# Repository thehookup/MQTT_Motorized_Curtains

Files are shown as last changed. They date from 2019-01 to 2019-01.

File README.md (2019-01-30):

# MQTT_Motorized_Curtains
Stepper motor controlled MQTT curtains - Home Assistant Integrated

## Initial Setup

1. Download the .ino file
2. Ensure you have the correct libraries download and installed (links at top of the ino file)
3. Update information in the user configuration section and upload to the NodeMCU
4. Hook up your NodeMCU, stepper driver and motor as shown in the wiring section
5. Send a value of 0 to the position MQTT topic which will be:

```c++
[USER_MQTT_CLIENT_NAME]/positionCommand
```
6. Send incrementally higher values to the position MQTT topic until your blinds are fully closed
7. Input that position value into the STEPS_TO_CLOSE field in the arduino sketch.
8. Send the updated file to your NodeMCU.

## Parts (Amazon Links)

Stepper Package 	        https://amzn.to/2MpRQPu

Pulleys	 	                https://amzn.to/2FLbCDI

Curtain Rope		          https://amzn.to/2U7h5Zs

Extruder Gear	 	          https://amzn.to/2T4QtrL

Bearings		              https://amzn.to/2U4bdQI

NodeMCU	                	https://amzn.to/2MkBcka

Buck Converter	 	        https://amzn.to/2FEcNFF

Power Supply		          https://amzn.to/2MmtFBj

M3 x 20mm	       	        Home Depot

#10 bolt	       	        Home Depot

## Wiring

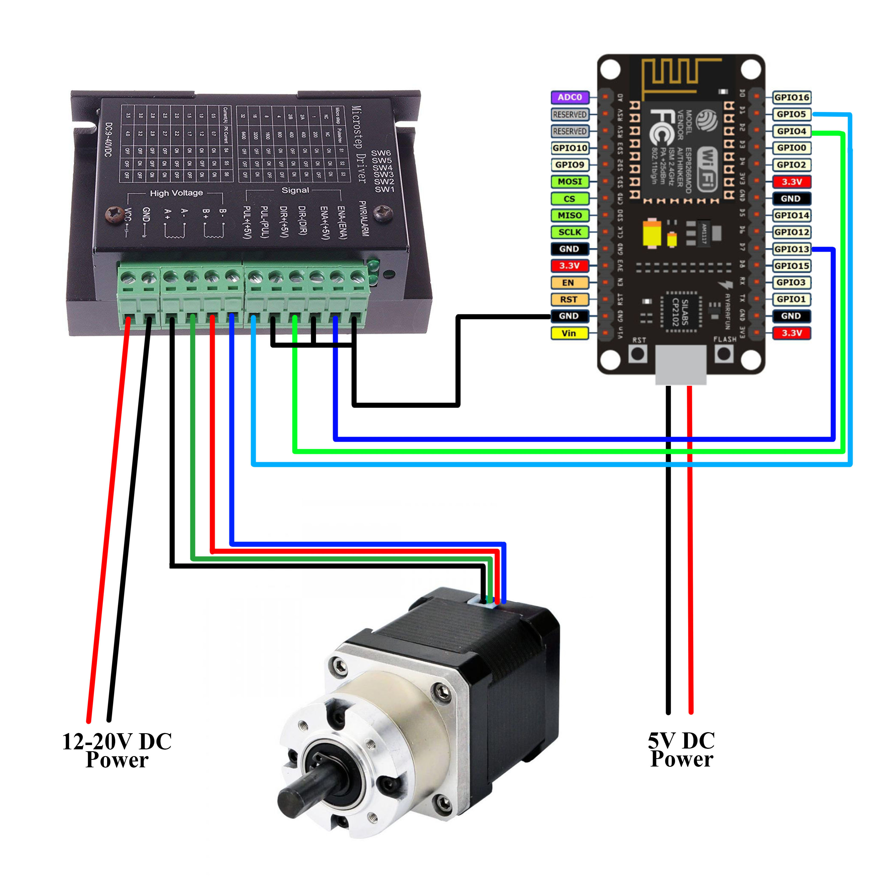
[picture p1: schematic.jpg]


## Stepper Dip Switch Positions

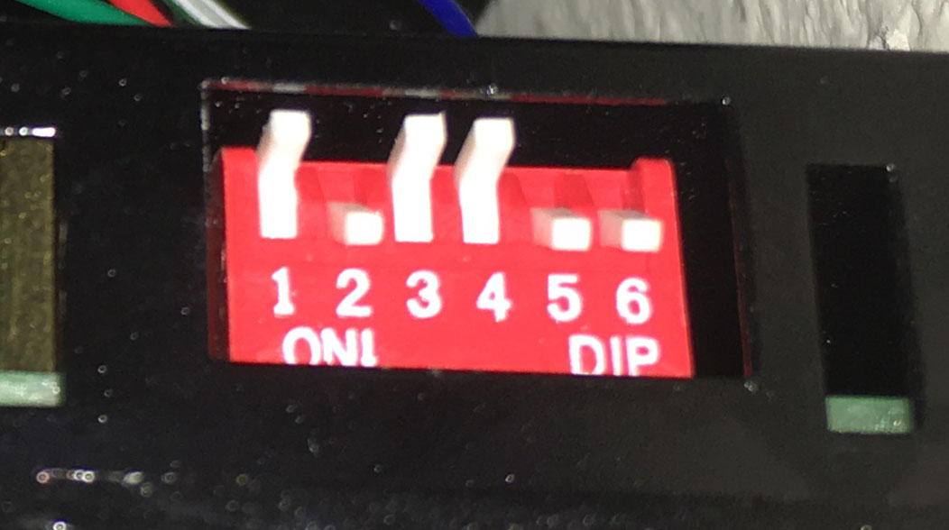
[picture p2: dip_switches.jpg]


## Motor Hardware Setup

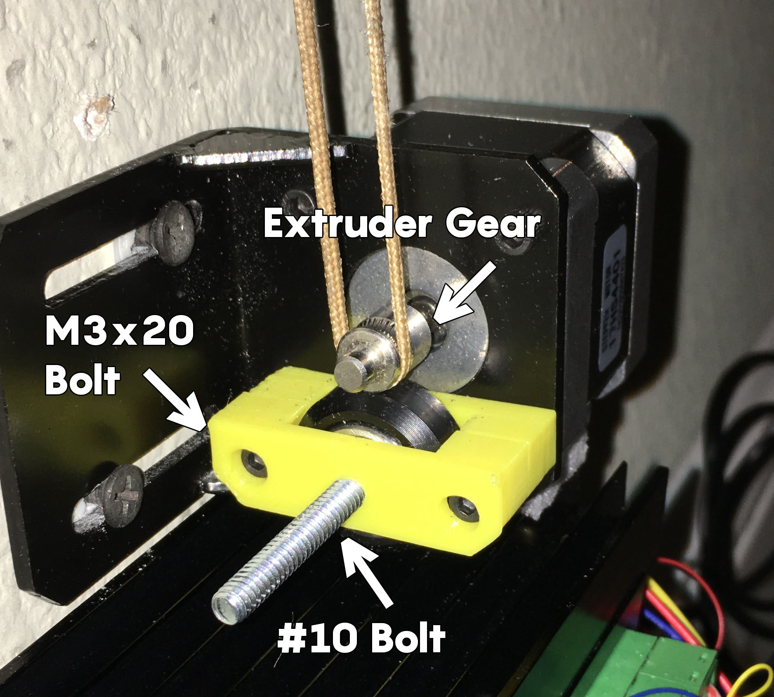
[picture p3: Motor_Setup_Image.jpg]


## Home Assistant YAML

```yaml
cover:
  - platform: mqtt
    name: "Downstairs Curtains"
    command_topic: "CurtainsMCU/command"
    set_position_topic: "CurtainsMCU/positionCommand"
    position_topic: "CurtainsMCU/positionState"
    state_topic: "CurtainsMCU/positionState"
    retain: true
    payload_open: "OPEN"
    payload_close: "CLOSE"
    payload_stop: "STOP"
    position_open: 88
    position_closed: 0
```

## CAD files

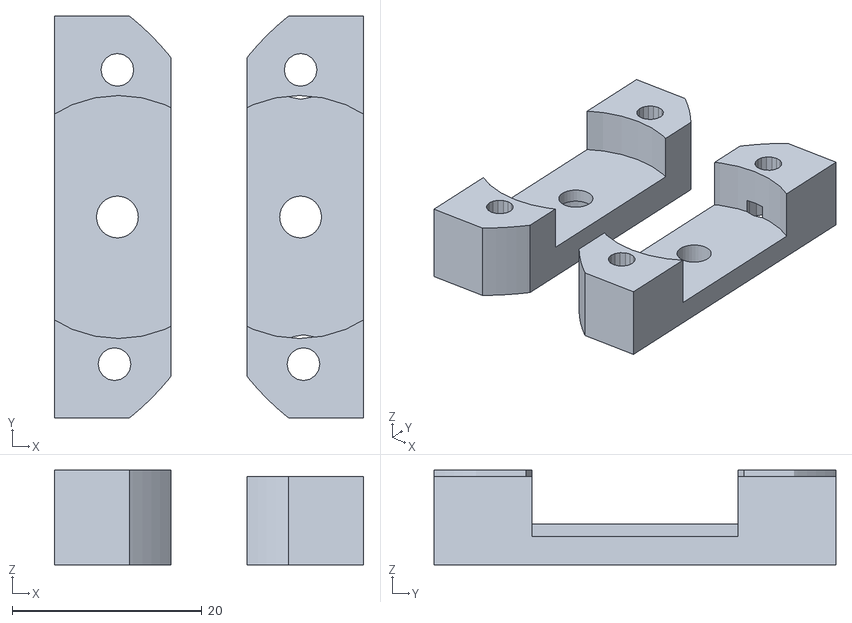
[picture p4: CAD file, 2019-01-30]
compact_direct_drive_extruder_v5.stl
32.5 x 42.3 x 10.00

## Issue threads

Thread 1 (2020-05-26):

Reducing steps...

stevetz, 2020-05-26:
Firstly, thanks so much for this and the video guide. I've successfully implemented our first motorised curtain following your instructions. I wondered if you'd found a way to stop/reduce the steps, as you mentioned in the video you might look at altering the ino to do this - the motor is obnoxiously loud, and with fewer or no wait periods it may get more WAF and let me do more!

DieKatzchen, 2020-12-04:
Could be done on an esp32 by running the MQTT code on one core and the motor code on the other. I might take a crack at it.

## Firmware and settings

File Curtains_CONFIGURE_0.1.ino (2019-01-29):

#include <SimpleTimer.h>    //https://github.com/marcelloromani/Arduino-SimpleTimer/tree/master/SimpleTimer
#include <ESP8266WiFi.h>    //if you get an error here you need to install the ESP8266 board manager 
#include <ESP8266mDNS.h>    //if you get an error here you need to install the ESP8266 board manager 
#include <PubSubClient.h>   //https://github.com/knolleary/pubsubclient
#include <ArduinoOTA.h>     //https://github.com/esp8266/Arduino/tree/master/libraries/ArduinoOTA
#include <AH_EasyDriver.h>  //http://www.alhin.de/arduino/downloads/AH_EasyDriver_20120512.zip

/*****************  START USER CONFIG SECTION *********************************/
/*****************  START USER CONFIG SECTION *********************************/
/*****************  START USER CONFIG SECTION *********************************/
/*****************  START USER CONFIG SECTION *********************************/

#define USER_SSID                 "YOUR_WIFI_SSID"
#define USER_PASSWORD             "YOUR_WIFI_PASSWORD"
#define USER_MQTT_SERVER          "YOUR MQTT SERVER"
#define USER_MQTT_PORT            1883
#define USER_MQTT_USERNAME        "YOUR_MQTT_LOGIN"
#define USER_MQTT_PASSWORD        "YOUR_MQTT_PASSWORD"
#define USER_MQTT_CLIENT_NAME     "CurtainsMCU"         // Used to define MQTT topics, MQTT Client ID, and ArduinoOTA

#define STEPPER_SPEED             300                   //Defines the speed in RPM for your stepper motor
#define STEPPER_STEPS_PER_REV     200                   //Defines the number of pulses that is required for the stepper to rotate 360 degrees
#define STEPPER_MICROSTEPPING     3                     //Defines microstepping 0 = no microstepping, 1 = 1/2 stepping, 2 = 1/4 stepping, 4 = 1/8 stepping
#define DRIVER_INVERTED_SLEEP     1                     //Defines sleep while pin high.  If your motor will not rotate freely when on boot, comment this line out.

#define STEPS_TO_CLOSE            88                    //Defines the number of steps needed to open or close fully

#define STEPPER_DIR_PIN           4                    //Marked as D2 on the NodeMCU
#define STEPPER_STEP_PIN          5                    //Marked as D1 on the NodeMCU
#define STEPPER_SLEEP_PIN         13                   //Marked as D7 on the NodeMCU
#define STEPPER_MICROSTEP_1_PIN   14                   //Does not need to be connected unless you want to dynamically change microstepping (not normal)
#define STEPPER_MICROSTEP_2_PIN   12                   //Does not need to be connected unless you want to dynamically change microstepping (not normal)
 
/*****************  END USER CONFIG SECTION *********************************/
/*****************  END USER CONFIG SECTION *********************************/
/*****************  END USER CONFIG SECTION *********************************/
/*****************  END USER CONFIG SECTION *********************************/
/*****************  END USER CONFIG SECTION *********************************/

WiFiClient espClient;
PubSubClient client(espClient);
SimpleTimer timer;
AH_EasyDriver shadeStepper(STEPPER_STEPS_PER_REV, STEPPER_DIR_PIN ,STEPPER_STEP_PIN,STEPPER_MICROSTEP_1_PIN,STEPPER_MICROSTEP_2_PIN,STEPPER_SLEEP_PIN);

//Global Variables
bool boot = true;
const int stepsPerRevolution = 200; 
int currentPosition = 0;
int newPosition = 0;
char positionPublish[50];
bool moving = false;
char charPayload[50];

const char* ssid = USER_SSID ; 
const char* password = USER_PASSWORD ;
const char* mqtt_server = USER_MQTT_SERVER ;
const int mqtt_port = USER_MQTT_PORT ;
const char *mqtt_user = USER_MQTT_USERNAME ;
const char *mqtt_pass = USER_MQTT_PASSWORD ;
const char *mqtt_client_name = USER_MQTT_CLIENT_NAME ; 




//Functions
void setup_wifi() {
  // We start by connecting to a WiFi network
  Serial.println();
  Serial.print("Connecting to ");
  Serial.println(ssid);

  WiFi.begin(ssid, password);

  while (WiFi.status() != WL_CONNECTED) {
    delay(500);
    Serial.print(".");
  }

  Serial.println("");
  Serial.println("WiFi connected");
  Serial.println("IP address: ");
  Serial.println(WiFi.localIP());
}

void reconnect() 
{
  int retries = 0;
  while (!client.connected()) {
    if(retries < 150)
    {
      Serial.print("Attempting MQTT connection...");
      if (client.connect(mqtt_client_name, mqtt_user, mqtt_pass)) 
      {
        Serial.println("connected");
        if(boot == false)
        {
          client.publish(USER_MQTT_CLIENT_NAME"/checkIn","Reconnected"); 
        }
        if(boot == true)
        {
          client.publish(USER_MQTT_CLIENT_NAME"/checkIn","Rebooted");
        }
        // ... and resubscribe
        client.subscribe(USER_MQTT_CLIENT_NAME"/command");
        client.subscribe(USER_MQTT_CLIENT_NAME"/positionCommand");
      } 
      else 
      {
        Serial.print("failed, rc=");
        Serial.print(client.state());
        Serial.println(" try again in 5 seconds");
        retries++;
        // Wait 5 seconds before retrying
        delay(5000);
      }
    }
    if(retries > 149)
    {
    ESP.restart();
    }
  }
}

void callback(char* topic, byte* payload, unsigned int length) 
{
  Serial.print("Message arrived [");
  String newTopic = topic;
  Serial.print(topic);
  Serial.print("] ");
  payload[length] = '\0';
  String newPayload = String((char *)payload);
  int intPayload = newPayload.toInt();
  Serial.println(newPayload);
  Serial.println();
  newPayload.toCharArray(charPayload, newPayload.length() + 1);
  if (newTopic == USER_MQTT_CLIENT_NAME"/command")
  {
    if (newPayload == "OPEN")
    {
      newPosition = STEPS_TO_CLOSE;
    }
    if (newPayload == "CLOSE")
    {
      newPosition = 0;
    }
    if (newPayload == "STOP")
    {
      newPosition = currentPosition;
    }
  }
  if (newTopic == USER_MQTT_CLIENT_NAME"/positionCommand")
  {
    if(boot == true)
    {
      newPosition = intPayload;
      currentPosition = intPayload;
      boot = false;
    }
    if(boot == false)
    {
      newPosition = intPayload;
    }
  }
  
}

void processStepper()
{
  if (newPosition > currentPosition)
  {
    #if DRIVER_INVERTED_SLEEP == 1
    shadeStepper.sleepON();
    #endif
    #if DRIVER_INVERTED_SLEEP == 0
    shadeStepper.sleepOFF();
    #endif
    shadeStepper.revolve(1);
    currentPosition++;
    moving = true;
  }
  if (newPosition < currentPosition)
  {
    #if DRIVER_INVERTED_SLEEP == 1
    shadeStepper.sleepON();
    #endif
    #if DRIVER_INVERTED_SLEEP == 0
    shadeStepper.sleepOFF();
    #endif
    shadeStepper.revolve(-1);
    currentPosition--;
    moving = true;
  }
  if (newPosition == currentPosition && moving == true)
  {
    #if DRIVER_INVERTED_SLEEP == 1
    shadeStepper.sleepOFF();
    #endif
    #if DRIVER_INVERTED_SLEEP == 0
    shadeStepper.sleepON();
    #endif
    String temp_str = String(currentPosition);
    temp_str.toCharArray(positionPublish, temp_str.length() + 1);
    client.publish(USER_MQTT_CLIENT_NAME"/positionState", positionPublish); 
    moving = false;
  }
  Serial.println(currentPosition);
  Serial.println(newPosition);
}

void checkIn()
{
  client.publish(USER_MQTT_CLIENT_NAME"/checkIn","OK"); 
}


//Run once setup
void setup() {
  Serial.begin(115200);
  shadeStepper.setMicrostepping(STEPPER_MICROSTEPPING);            // 0 -> Full Step                                
  shadeStepper.setSpeedRPM(STEPPER_SPEED);     // set speed in RPM, rotations per minute
  #if DRIVER_INVERTED_SLEEP == 1
  shadeStepper.sleepOFF();
  #endif
  #if DRIVER_INVERTED_SLEEP == 0
  shadeStepper.sleepON();
  #endif
  WiFi.mode(WIFI_STA);
  setup_wifi();
  client.setServer(mqtt_server, mqtt_port);
  client.setCallback(callback);
  ArduinoOTA.setHostname(USER_MQTT_CLIENT_NAME);
  ArduinoOTA.begin(); 
  delay(10);
  timer.setInterval(((1 << STEPPER_MICROSTEPPING)*5800)/STEPPER_SPEED, processStepper);   
  timer.setInterval(90000, checkIn);
}

void loop() 
{
  if (!client.connected()) 
  {
    reconnect();
  }
  client.loop();
  ArduinoOTA.handle();
  timer.run();
}

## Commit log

2019-01-29 Wiring Schematic
2019-01-29 Dip switch positions for 1/8 stepping
2019-01-30 STL file for 3D printing the bearing tensioner
    [compact_direct_drive_extruder_v5.stl]
2019-01-30 Image of motor
